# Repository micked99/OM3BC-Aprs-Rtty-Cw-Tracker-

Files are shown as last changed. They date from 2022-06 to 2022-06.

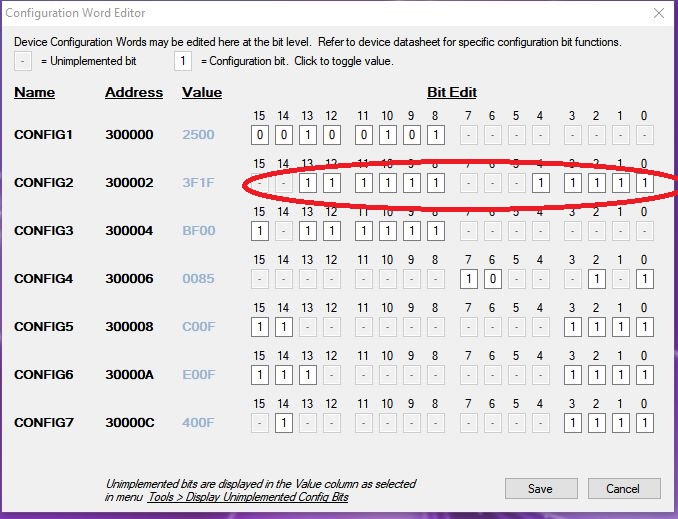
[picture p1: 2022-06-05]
!!1.9V Bor wdt2min14s.jpg

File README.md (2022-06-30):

# OM3BC-Aprs-Rtty-Cw-Tracker-
OM3BC Aprs-Rtty-Cw Tracker 
OM3BC tracker info
Some extended information about the OM3BC tracker found here: www.om3bc.com/docs/payload/payload_en
nQnfMv6

Some extended information about the OM3BC tracker found here: www.om3bc.com/docs/payload/payload_en
My aim of the Eagle files is to make an as simple to build, cheap and light tracker as possible, a fully assambled board should weigh in on about 1 - 1.3gram,
a fully assambled board with solar cells and antenna about 3.5gram

Im using 6 of the smallest avalible (19x39mm) solar cells in series to power the board, it makes it run from and to 15-19° solar angle depending on Gps used

After more then 25 launches over the years and probably more then 10 pcb revisions I have come to this final? design, the intention of this page is to ease the building and configuring the OM3BC APRS / RTTY / CW tracker.

The rar file below contains all files mentioned in this small writeup

There are two different firmware versions depending on what Gps module you intend to use:

fw7.5 should be used with Ublox Max modules, I have so far only tested the Max7q and Max7c both working well,
the low voltage "c" version getting a bit longer "runtime" due to its lower voltage demands, Max 6 & 8 should work just as well.

fw14 should be used with ATGM336 Gps which is a "new" cheap module that can be found for around $3 on Aliexpress,
there is no flightmode that needs to be set on this module, it have been tested to over 32000m at the time of this write up.

You will also find Eagle pcb files in the rar for two types of PIC ic footprints.

I have tested both the L version and LF version of the PIC but could not see any advantages using the low voltage (LF) version of the ic

All versions of the si4x6x I have tried have worked well, so far I have tested SI4060, 4463 and 4063.

THE MOST important setting to get reliable startup of the board is to enable the Watch Dog Timer (WDT) you set all as 1:s as in the below picture.
To do this you press the "Configuration:" in the PICkit3 before you program the board.
!!1 9V Bor wdt2min14s
You can read about the fuses in the pic18f26k22.pdf (rar)

Schematic
XS

Settings Im using:
MYC SA6BSS-9
DEVIATION 425
POUT 8 (pout 100 using 4060 // pout 8 = 25mW on a 4x63)
APRS on
HOLD 2
TAIL on 2
INTEMP yes REF 19199985
UBLOX on (=atgm336)
TTEXT RTTY 434.5/100b7n2 Temp:\W Gps:\B
UNPROTO APRS V wide0-0 // = to not use digipeaters, leave unchanged if you want to use digipeaters
RFRQ 434500000 // putting the rtty up in ism band

Im using Termite terminal to setup the board, this as well as well as the PICkit3 is in the rar, termite also supports macros so you dont have to enter every setting everytime you setup a new board.

When you configure the board you have to use a rs232 programmer, the only one so far that works reliably is this type, look for it on ebay or aliexpress,
should cost arround 3-5$, note the DC jack, electrolytic caps and LEDs
The voltage out from this is 5V, to reduce this you can put 2 diods in series on the VCC to lower the voltage to more reasonable levels, or preferably a 3.3V LDO.

s-l1600

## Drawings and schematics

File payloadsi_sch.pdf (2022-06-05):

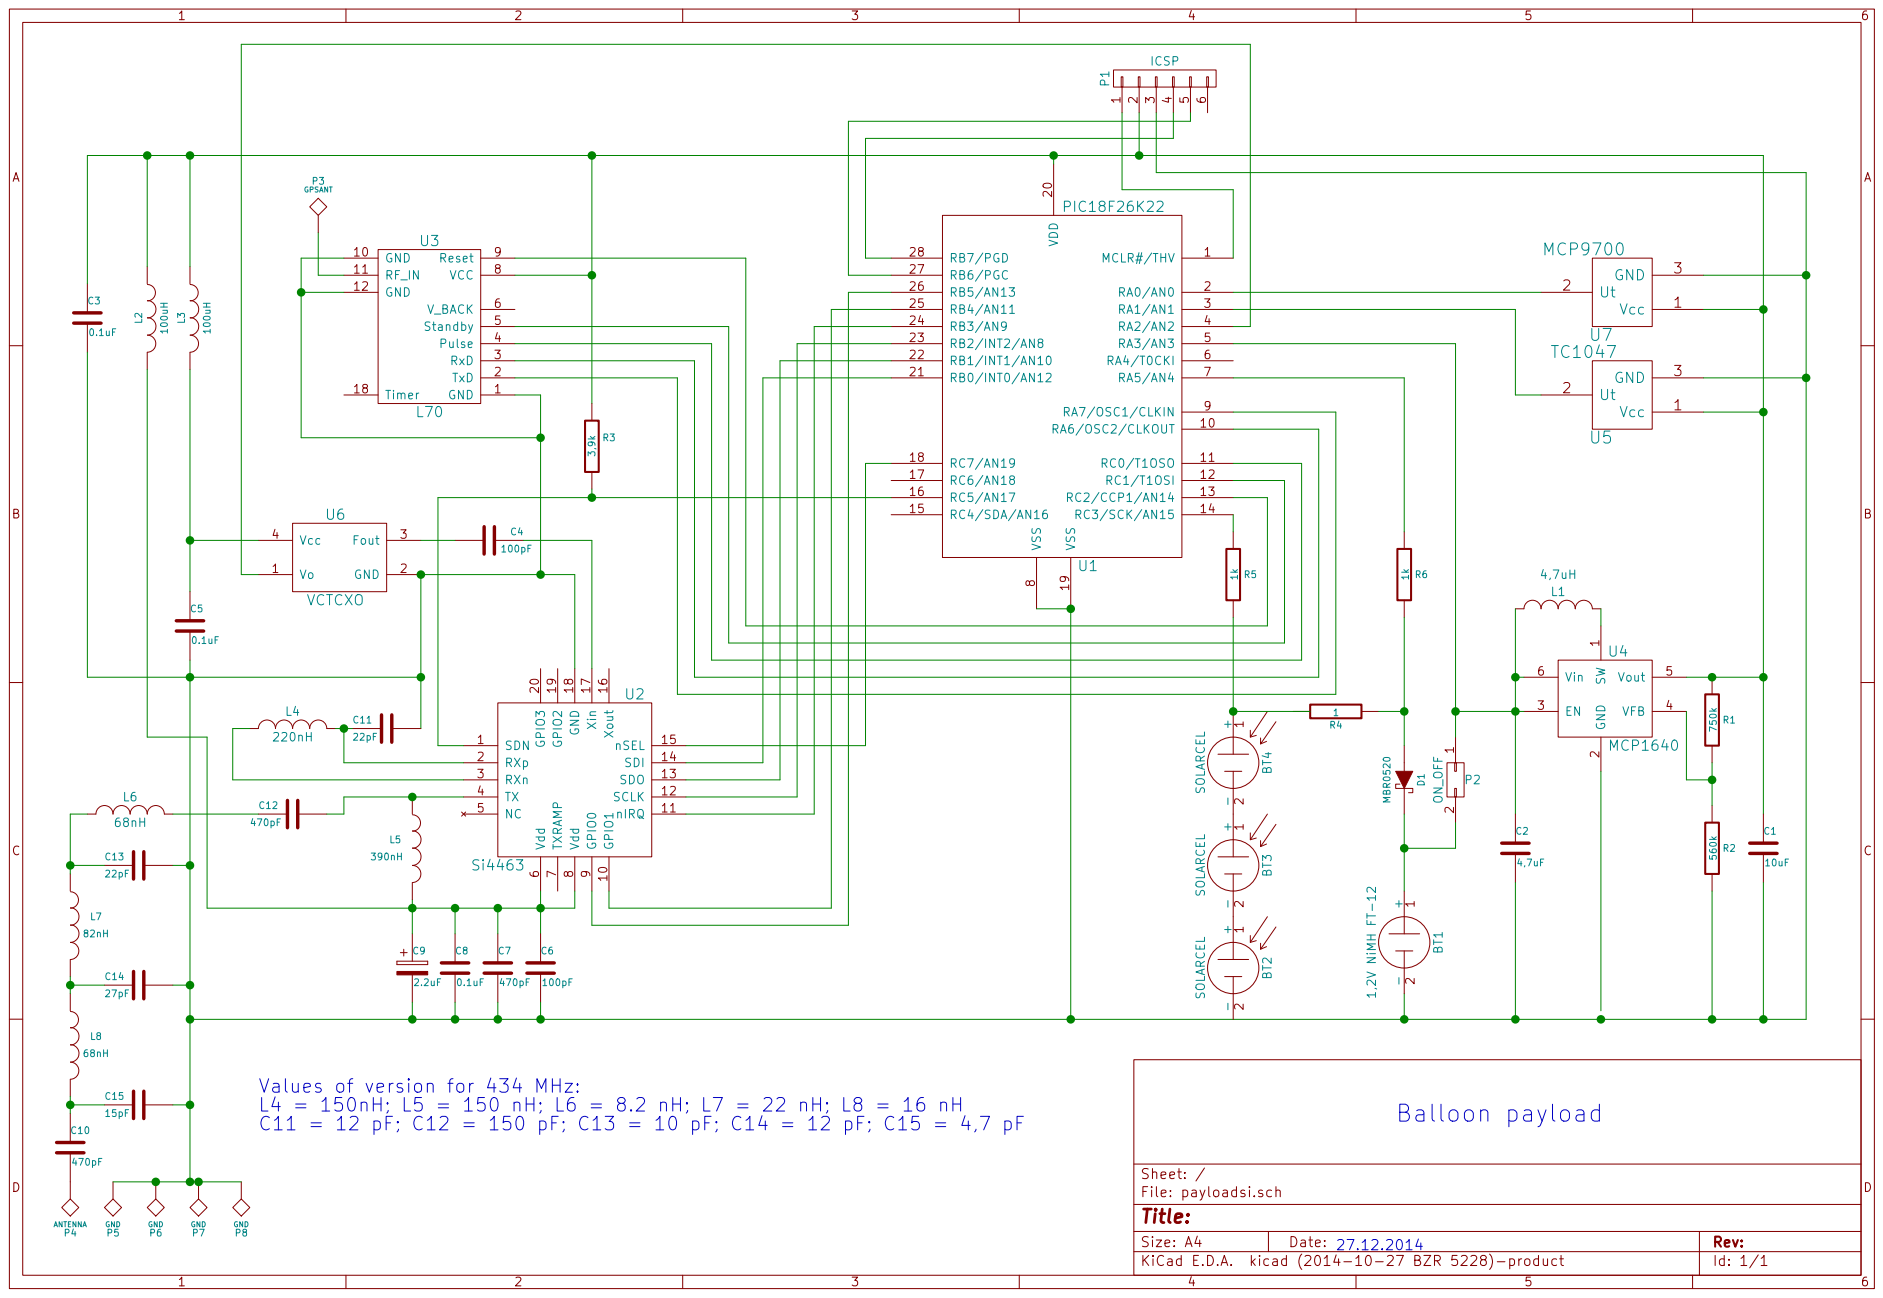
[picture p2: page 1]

8 RA7/OSC1/CLKIN 9 RA6/OSC2/CLKOUT 10 VDD 20 RC0/T1OSO 11 RB0/INT0/AN12 21 RC1/T1OSI 12 RB1/INT1/AN10 22 RC2/CCP1/AN14 13 RB2/INT2/AN8 23 RC3/SCK/AN15 14 RB3/AN9 24 RC4/SDA/AN16 15 RB4/AN11 25 RC5/AN17 16 RB5/AN13 26 RC6/AN18 17 RB6/PGC 27 RC7/AN19 18 RB7/PGD 28 VSS 19 U1 PIC18F26K22

2 EN 3 VFB 4 Vout 5 Vin 6 U4MCP1640

File: payloadsi.sch Sheet: /
Id: 1/1 Title:

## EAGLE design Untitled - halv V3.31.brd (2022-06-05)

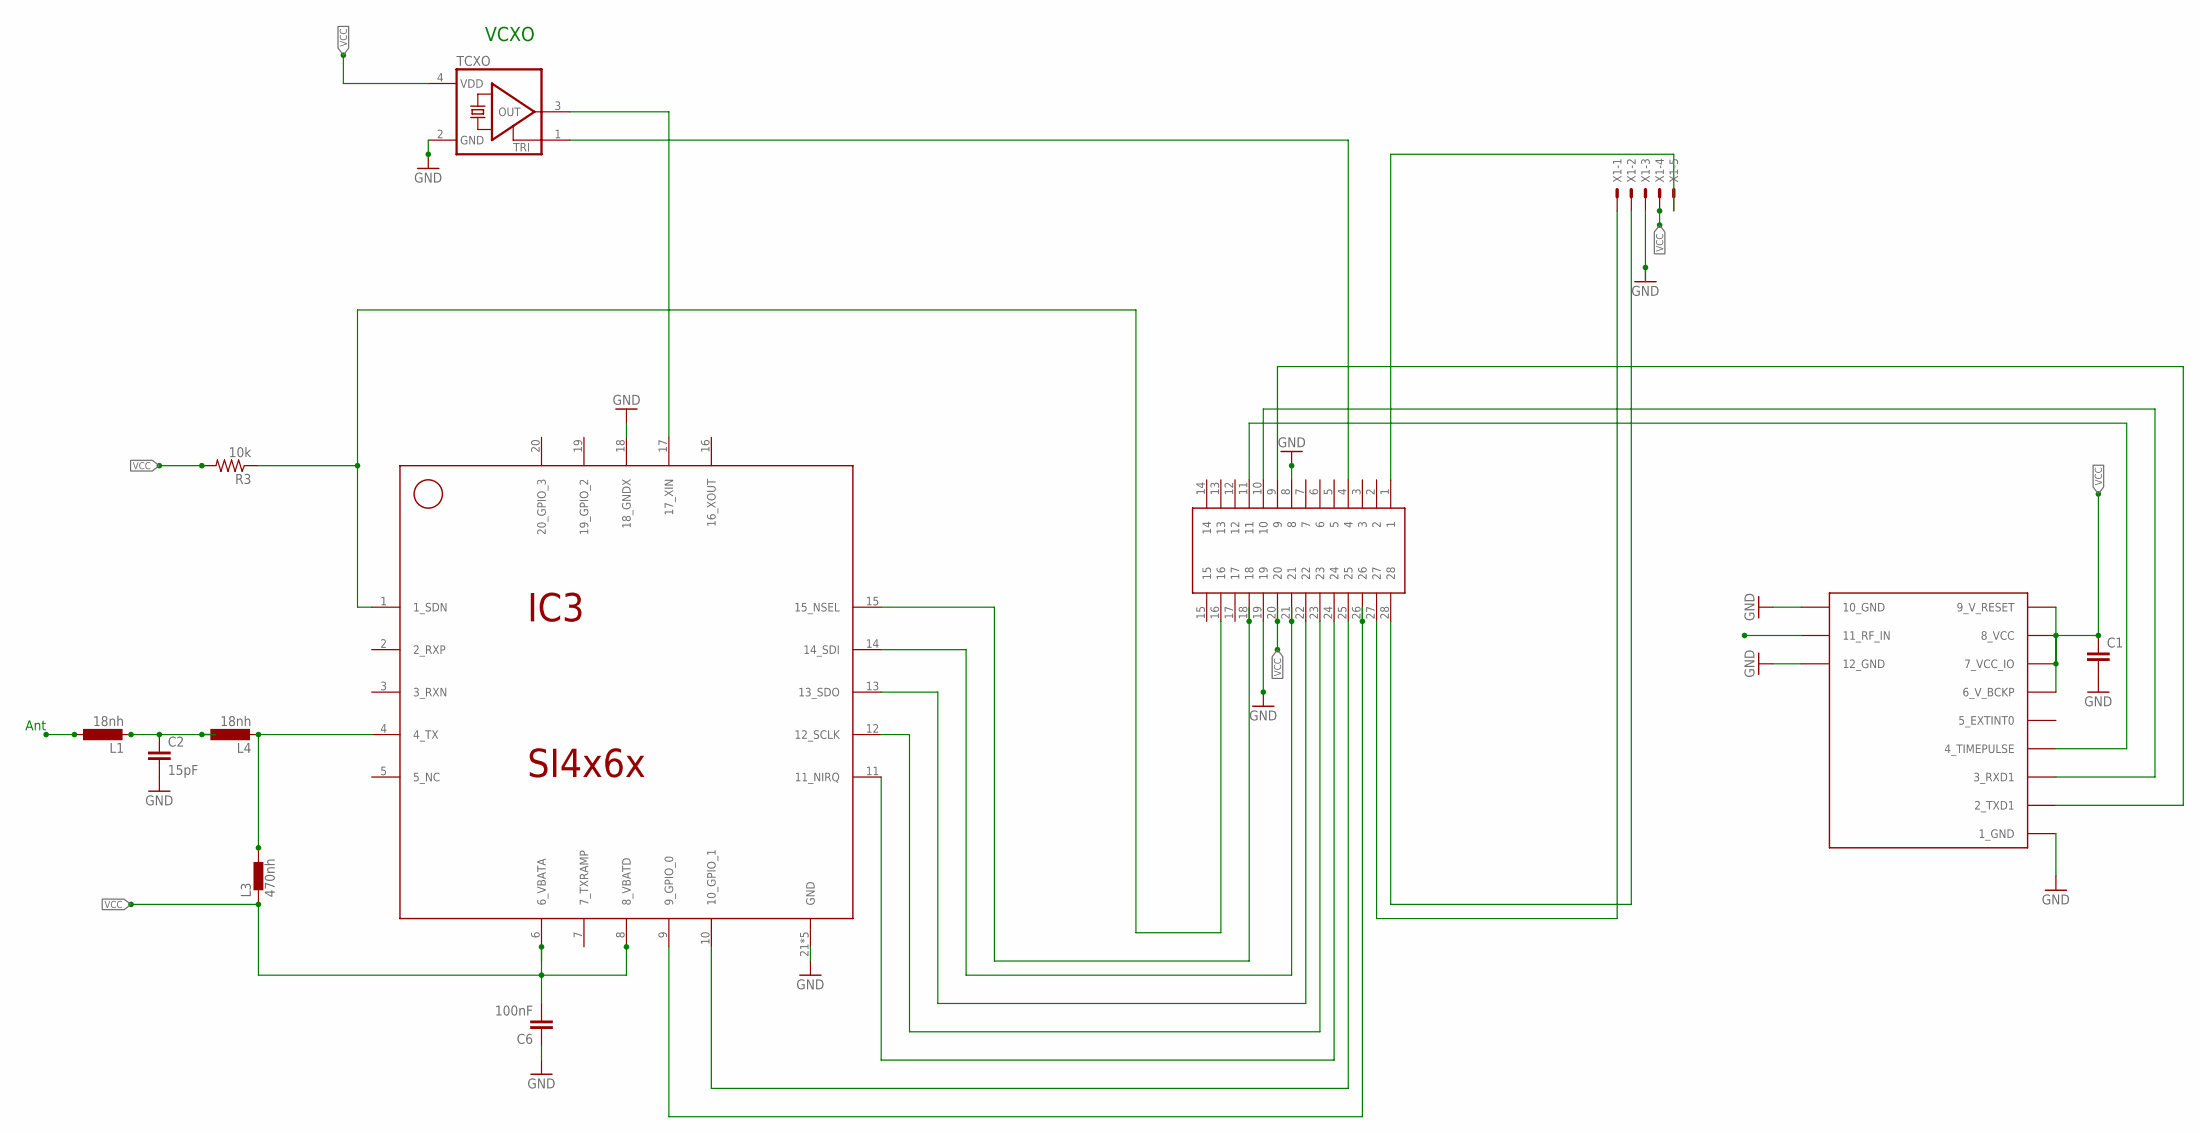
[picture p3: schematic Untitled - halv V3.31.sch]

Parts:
C1: CC0603; C0603
C2: 15pF; C0603K
C6: 100nF; C0402
IC3: SI4x6x; QFN-20
L1, L4: 18nh; L2012C
L3: 470nh; 0402
PIC-VERS3.3: SSOP28; SSOP28DB
R3: 10k; R0402
TCXO: CRYSTAL_3.2X2.5-TCXO
U$1: UBLOX_MAX
X1: 22-23-2051

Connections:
ANT: U$1.11_RF_IN
GND: C1.2, C2.2, C6.1, IC3.18 (18_GNDX), IC3.21 (GND), IC3.22 (GND), IC3.23 (GND), IC3.24 (GND), IC3.25 (GND), PIC-VERS3.3.8, PIC-VERS3.3.19, TCXO.2 (GND), U$1.1_GND, U$1.10_GND, U$1.12_GND, X1.3
unnamed: PIC-VERS3.3.1, X1.5
unnamed: PIC-VERS3.3.28, X1.2
unnamed: PIC-VERS3.3.27, X1.1
unnamed: IC3.9 (9_GPIO_0), PIC-VERS3.3.26
unnamed: IC3.10 (10_GPIO_1), PIC-VERS3.3.25
unnamed: IC3.11 (11_NIRQ), PIC-VERS3.3.24
unnamed: IC3.12 (12_SCLK), PIC-VERS3.3.23
unnamed: IC3.13 (13_SDO), PIC-VERS3.3.22
unnamed: IC3.14 (14_SDI), PIC-VERS3.3.21
unnamed: IC3.15 (15_NSEL), PIC-VERS3.3.18
unnamed: IC3.17 (17_XIN), TCXO.3 (OUT)
unnamed: IC3.4 (4_TX), L3.2, L4.2
unnamed: PIC-VERS3.3.4, TCXO.1 (TRI)
unnamed: PIC-VERS3.3.11, U$1.4_TIMEPULSE
unnamed: PIC-VERS3.3.10, U$1.3_RXD1
unnamed: C2.1, L1.2, L4.1
unnamed: PIC-VERS3.3.9, U$1.2_TXD1
RADIO_SDN: IC3.1 (1_SDN), PIC-VERS3.3.16, R3.1
VCC: C1.1, C6.2, IC3.6 (6_VBATA), IC3.8 (8_VBATD), L3.1, PIC-VERS3.3.20, R3.2, TCXO.4 (VDD), U$1.6_V_BCKP, U$1.7_VCC_IO, U$1.8_VCC, U$1.9_V_RESET, X1.4

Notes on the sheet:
VCXO
Ant

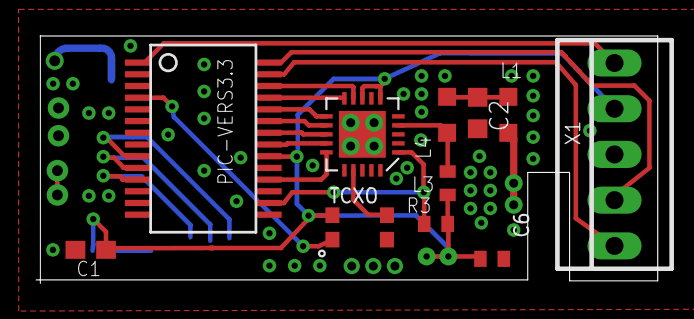
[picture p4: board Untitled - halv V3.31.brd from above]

Board: 2 copper layers, 34.5 x 13.7 mm, 12 parts (1 on the bottom side), 20 nets.

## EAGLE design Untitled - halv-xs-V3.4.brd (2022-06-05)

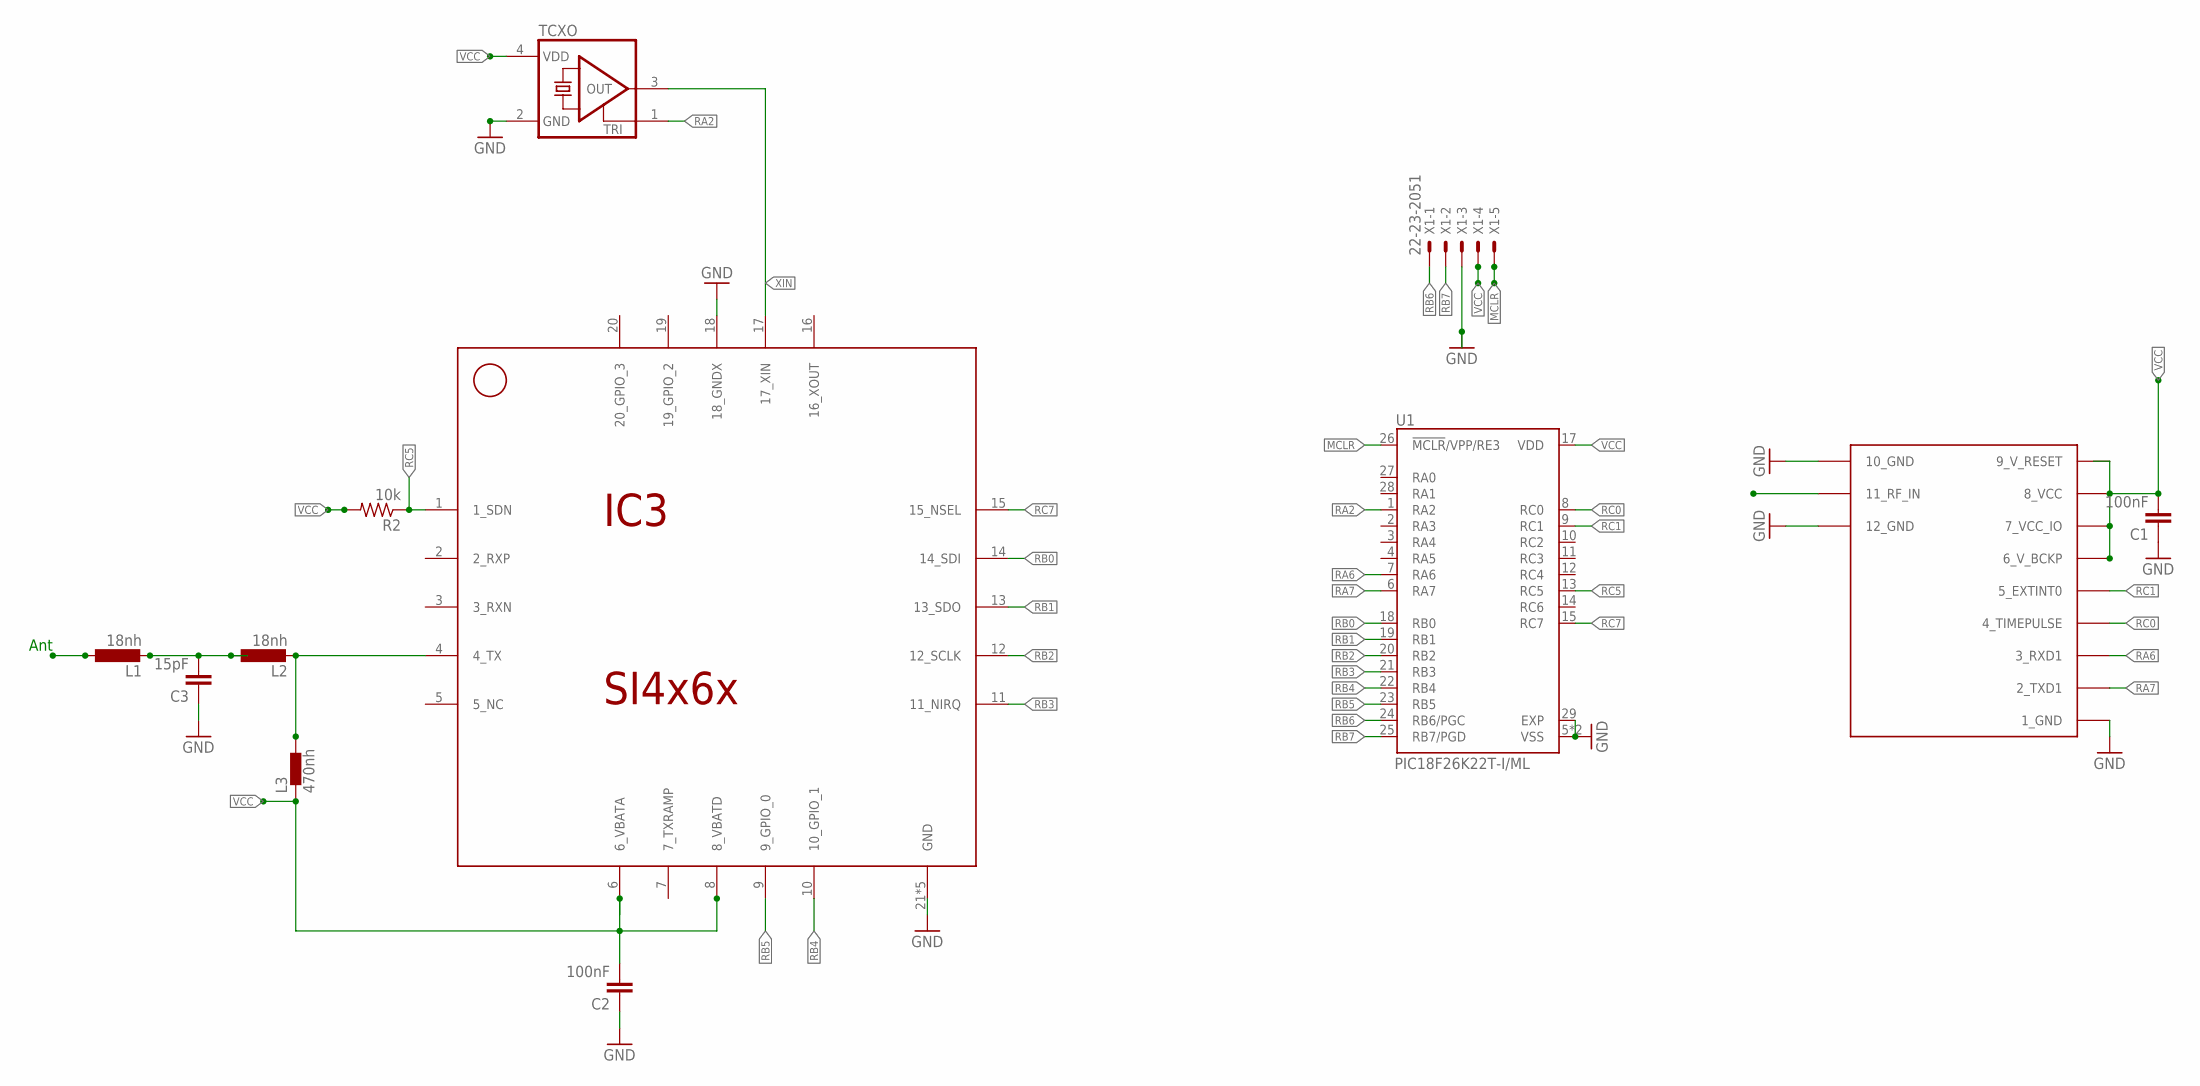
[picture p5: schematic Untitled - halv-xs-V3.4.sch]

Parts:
C1, C2: 100nF; C0402
C3: 15pF; C0402
IC3: SI4x6x; QFN-20
L1, L2: 18nh; L2012C
L3: 470nh; 0402
R2: 10k; R0402
TCXO: CRYSTAL_3.2X2.5-TCXO
U1: PIC18F26K22T-I/ML; QFN65P600X600X100-29N
U$1: UBLOX_MAX
X1: 22-23-2051

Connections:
ANT: U$1.11_RF_IN
GND: C1.1, C2.1, C3.1, IC3.18 (18_GNDX), IC3.21 (GND), IC3.22 (GND), IC3.23 (GND), IC3.24 (GND), IC3.25 (GND), TCXO.2 (GND), U1.5 (VSS), U1.16 (VSS), U1.29 (EXP), U$1.1_GND, U$1.10_GND, U$1.12_GND, X1.3
MCLR: U1.26 (!MCLR!/VPP/RE3), X1.5
unnamed: C3.2, L1.2, L2.1
RA2: TCXO.1 (TRI), U1.1 (RA2)
RA6: U1.7 (RA6), U$1.3_RXD1
RA7: U1.6 (RA7), U$1.2_TXD1
RB0: IC3.14 (14_SDI), U1.18 (RB0)
RB1: IC3.13 (13_SDO), U1.19 (RB1)
RB2: IC3.12 (12_SCLK), U1.20 (RB2)
RB3: IC3.11 (11_NIRQ), U1.21 (RB3)
RB4: IC3.10 (10_GPIO_1), U1.22 (RB4)
RB5: IC3.9 (9_GPIO_0), U1.23 (RB5)
RB6: U1.24 (RB6/PGC), X1.1
RB7: U1.25 (RB7/PGD), X1.2
RC0: U1.8 (RC0), U$1.4_TIMEPULSE
RC1: U1.9 (RC1), U$1.5_EXTINT0
RC5: IC3.1 (1_SDN), R2.1, U1.13 (RC5)
RC7: IC3.15 (15_NSEL), U1.15 (RC7)
TX: IC3.4 (4_TX), L2.2, L3.2
VCC: C1.2, C2.2, IC3.6 (6_VBATA), IC3.8 (8_VBATD), L3.1, R2.2, TCXO.4 (VDD), U1.17 (VDD), U$1.6_V_BCKP, U$1.7_VCC_IO, U$1.8_VCC, U$1.9_V_RESET, X1.4
XIN: IC3.17 (17_XIN), TCXO.3 (OUT)

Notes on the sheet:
Ant

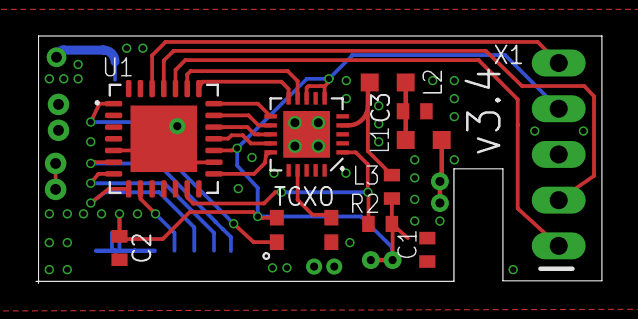
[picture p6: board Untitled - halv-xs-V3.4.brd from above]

Board: 2 copper layers, 31.4 x 13.7 mm, 12 parts (1 on the bottom side), 21 nets.
